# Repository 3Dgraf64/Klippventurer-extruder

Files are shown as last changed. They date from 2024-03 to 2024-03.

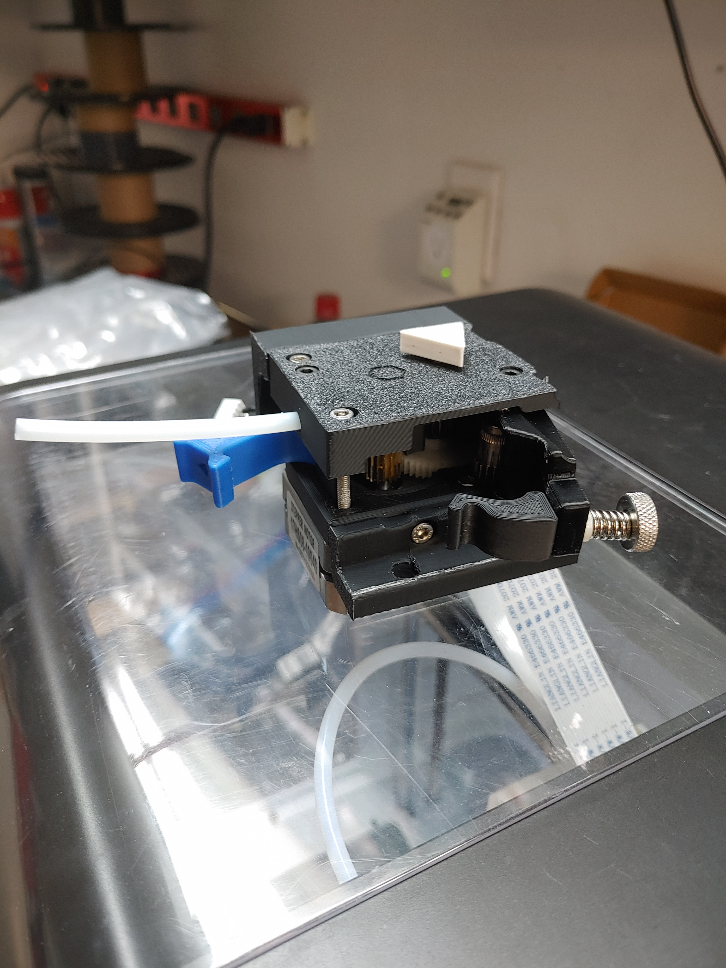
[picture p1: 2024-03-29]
Images/20240329_131136[1].jpg

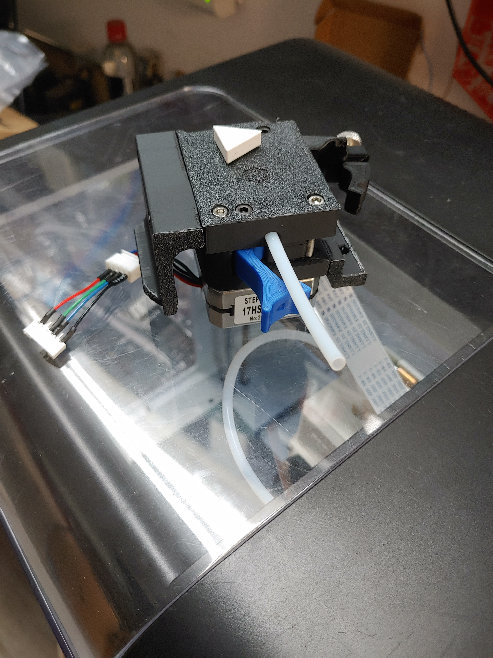
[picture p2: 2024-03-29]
Images/20240329_131118[1].jpg

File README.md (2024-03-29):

# Klippventurer-mods
!!IN PROGRESS!!

This is my contribution to the Klippventurer project.
A big thank you to The-Synthax for being involved in this project by giving us the opportunity to replace the firmware of this printer by Klipper.
Check out here: https://github.com/synthread/Klippventurer

In my Adventurer 3 printer upgrade process, the next step after upgrading the operating system to Klipper (Klippventurer) is to replace the extruder.
I had an old Voron Clockwork extruder lying around.  So I decided to go from there.  Original Voron's .step files where edited in FreeCad.
The result is an extruder whose internal parts are those of the Clockwork but whose fasteners are modified.

Printing:

The printing parameters are those prescribed by Voron: ABS, layer height 0.2mm, extrusion width 0.4,
filling 40%, grid type filling..., walls 4, upper/ lower layers 5 and no support.
For the legs I suggest a skirt.  Cut the parts in triangle.  These are supports.

Hardware and assembly:

The hardware and assembly is essentially the same as Voron’s:
https://github.com/VoronDesign/Voron-Afterburner/blob/afterburner/Manual/Afterburner.pdf
The main differences are the attachment of the legs and an ECAS coupler.
I did an adapter to connect the motor.
The target is held by 2 3x6mm magnets. 

Config:
You'll have to modify your 
rotation_distance: 39.461375 and
gear_ratio: 50:10.  
You may also have to reverse the rotation: dir_pin: !PA2

Tests:
Preliminary test shows 15mm3/sec with a .4mm CHT nozzle at 225 degc PLA

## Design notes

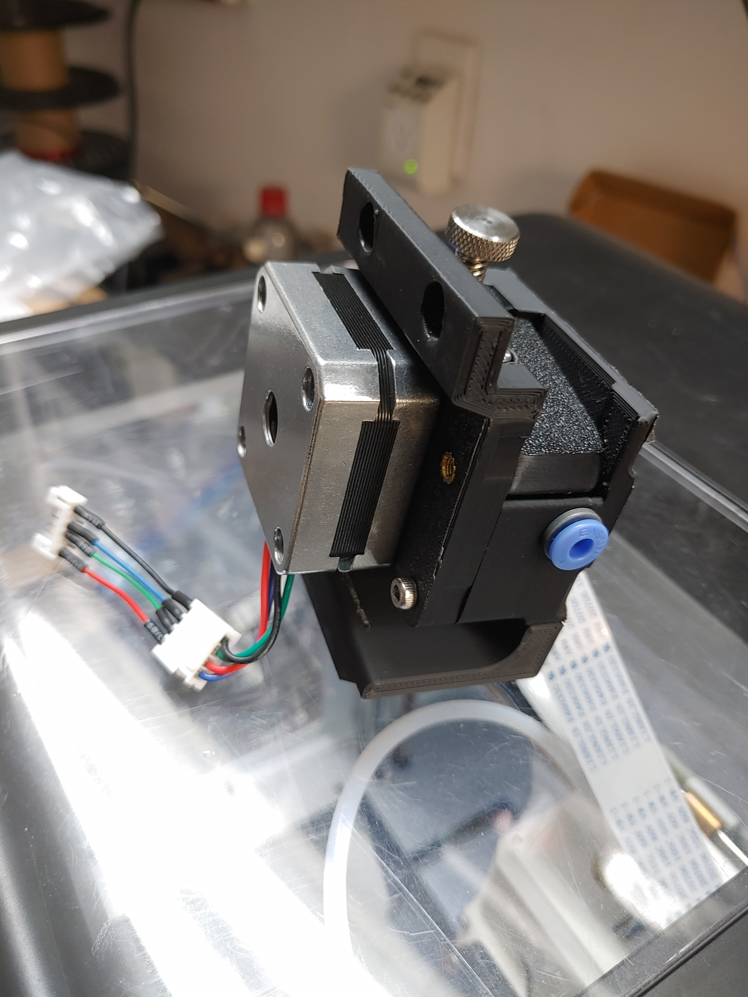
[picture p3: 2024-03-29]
Images/20240329_131154[1].jpg

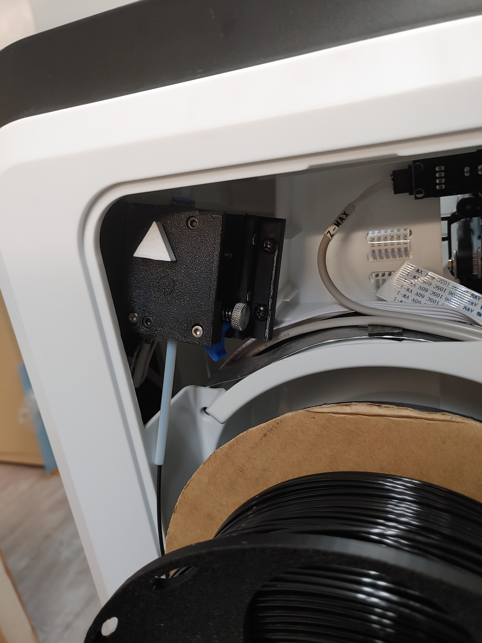
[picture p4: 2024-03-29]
Images/20240329_131842[1].jpg

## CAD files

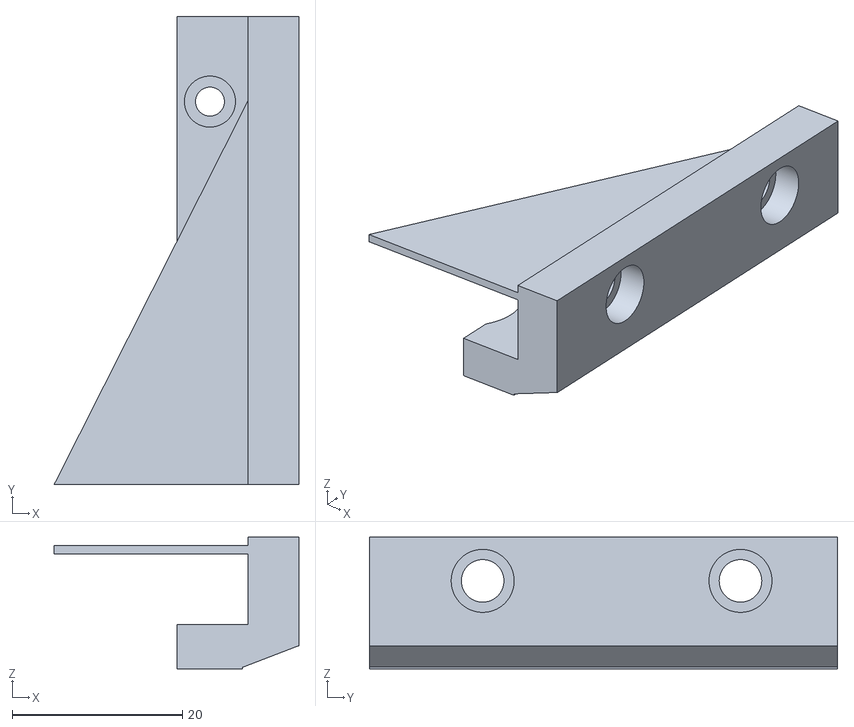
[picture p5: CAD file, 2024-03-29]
STLs/Right leg.stl
28.8 x 55.0 x 15.5

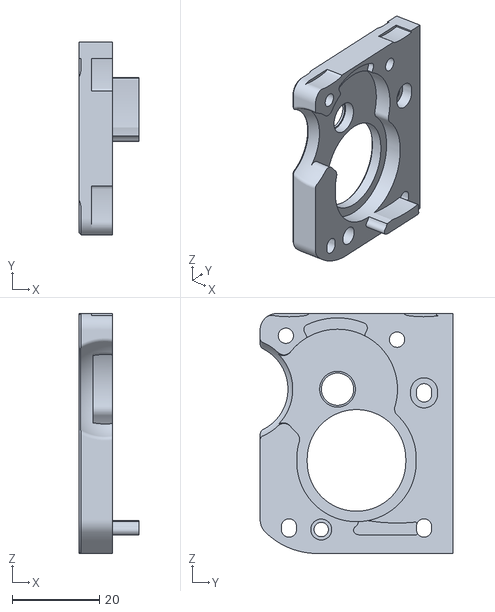
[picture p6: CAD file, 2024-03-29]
STLs/Motor plate.stl
13.7 x 44.2 x 55.0

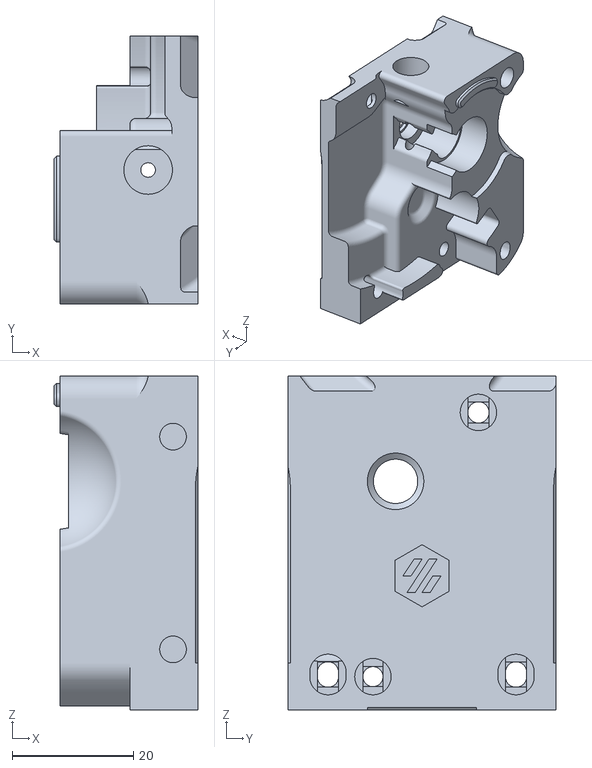
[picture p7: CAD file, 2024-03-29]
STLs/Front body.stl
23.7 x 44.2 x 55.0

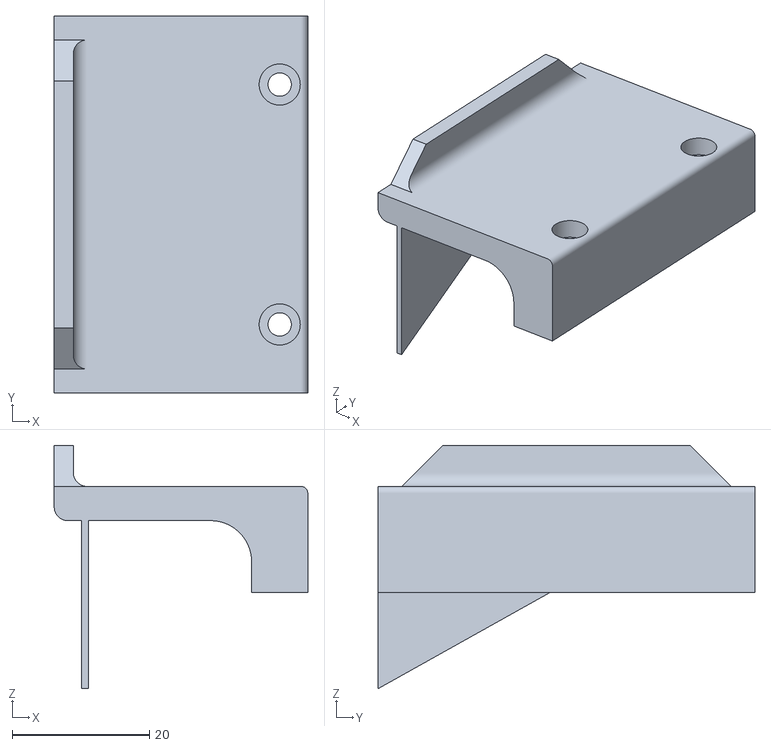
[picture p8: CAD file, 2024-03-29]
STLs/Left leg.stl
37.0 x 55.0 x 35.5

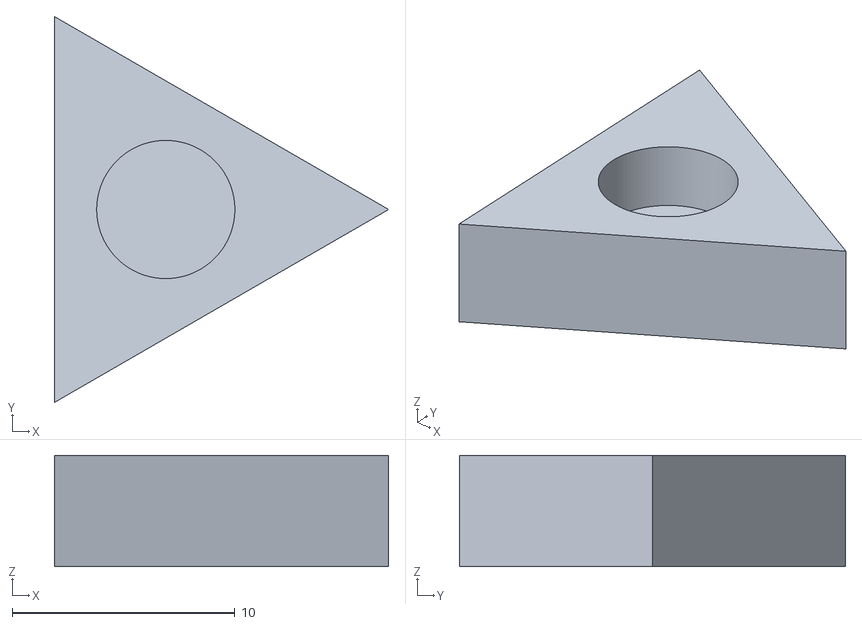
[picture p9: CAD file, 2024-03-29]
STLs/Target.stl
15.0 x 17.3 x 5.00

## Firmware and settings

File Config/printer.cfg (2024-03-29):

# This file contains pin mappings for Adventurer 3 and MonoPrice Voxel with SZ16 mainboard
# There may be versions of these printers that require slight modifications to the config.
# To use this config, the firmware should be compiled for the STMicroelectronics STM32,
# Processor model STM32F103, Clock Reference 12 MHz crystal, Serial on USART1 PA10/PA9.
# To install Klipper, you must follow the steps as described here:
# https://github.com/synthread/Klippventurer

# See docs/Config_Reference.md for a description of parameters.
# If you have TMC2209 drivers (like Adventurer 3 Pro) replace all instances of TMC2208 in this config with TMC2209
[include adv3-macros.cfg]
[include fluidd.cfg]
[include KAMP_Settings.cfg]
[exclude_object]

[mcu]
serial: /dev/ttyAMA0
baud: 250000
restart_method: command
#[mcu rpi]
#serial: /tmp/klipper_host_mcu

[printer]
kinematics: cartesian
max_velocity: 800
square_corner_velocity: 6
max_accel: 6500
max_z_velocity: 30
max_z_accel: 400

[stepper_x]
step_pin: PB8
dir_pin: !PB9
enable_pin: !PB7
microsteps: 32
rotation_distance: 33.9
endstop_pin: ^PC14
position_endstop: 159 # Set this to the distance between the endstop trigger point and touching the left side of the axis
position_max: 161 # Set this to the distance between the endstop and touching the right side of the axis, PLUS position_endstop
position_min: 0 # Leave this alone
homing_speed: 75

[stepper_y]
step_pin: PC1
dir_pin: !PC2
enable_pin: !PC0
microsteps: 32
rotation_distance: 33.9
endstop_pin: ^PB3
position_endstop: 4 # Set this to the distance between the endstop trigger point and touching the back side of the axis
position_max: 151 # Set this to the distance between the endstop and touching the front side of the axis
homing_speed: 75

[stepper_z]
step_pin: PC8
dir_pin: !PC9
enable_pin: !PC7
microsteps: 16
rotation_distance: 6.25
endstop_pin: !PC13
position_min: -2 # This is slightly lower than the bed surface to allow for mesh leveling
#position_endstop: 148 # Leave this alone, use fluidd to calibrate your Z offset.
position_max: 155 # Set this to the distance between the endstop trigger point and touching the top of the axis. If you see the axis skew diagonally at this position, it's too high
homing_speed: 25
second_homing_speed: 15

[thermistor adv3_ntc]
temperature1: 19
resistance1:  123000
temperature2: 79
resistance2:  5820 
temperature3: 230
resistance3:  255 

[extruder]
step_pin: PA1
dir_pin: !PA2
enable_pin: !PA3
microsteps: 16
full_steps_per_rotation: 200
gear_ratio: 50:10
rotation_distance: 39.461375
nozzle_diameter: 0.4
filament_diameter: 1.750
heater_pin: PA8
max_power: 0.8
sensor_type: ATC Semitec 104NT-4-R025H42G
sensor_pin: PA5
min_temp: 10
max_temp: 270
min_extrude_temp: 10
#control = pid
#pid_kp = 26.213
#pid_ki = 1.304
#pid_kd = 131.721
max_extrude_only_distance: 550
max_extrude_only_velocity: 2000
max_extrude_cross_section: 5
pressure_advance: 1.2
pressure_advance_smooth_time: 0.1

[heater_bed]
heater_pin: PC6
sensor_type: adv3_ntc
sensor_pin: PC4
min_temp: 0
max_temp: 110

[temperature_sensor mcu_temp]
sensor_type: temperature_mcu
#this is the operational temperature range of STM32f103
min_temp: -40
max_temp: 85
[temperature_sensor Pi_2W]
sensor_type: temperature_host
min_temp: 10
max_temp: 100
# Part cooling fan and heatbreak fan
#[fan]
#pin: PB10
#cycle_time: 0.1
[heater_fan Fan_hotend]
##	Hotend Fan - CNC_FAN1
pin: PB10
max_power: 1.0
kick_start_time: 0.5
heater: extruder
heater_temp: 50.0
##	If you are experiencing back flow, you can reduce fan_speed
shutdown_speed:1.0

# Mainboard cooling fan
[controller_fan mainboard]
pin: PA4
heater: extruder, heater_bed

# Chamber ventilation fan
#[fan_generic chamber_fan]
#pin: PB13
#cycle_time: 0.1

[output_pin led]
pin: PB12
value: 1
pwm: true
cycle_time: 0.008333 # This PWM frequency should stop the LED from flickering on video

[homing_override]
axes: zxy
gcode:
 g28 z
 g28 x
 g28 y

[bed_mesh]
speed: 100
horizontal_move_z: 5
mesh_min: 5, 5
mesh_max: 150, 145
probe_count: 3, 3
fade_start: 1
fade_end: 10
fade_target: 0

[input_shaper]
shaper_freq_x: 205
shaper_type: mzv
shaper_freq_y: 197.126
shaper_type: ei

[firmware_retraction]
retract_length: 3.8
retract_speed: 25
unretract_extra_length: 0
unretract_speed: 25

########################################
# TMC2208 configuration
########################################

[tmc2208 stepper_x]
uart_pin: PC10
select_pins: !PB0, !PB1, !PD1
run_current: 0.600
sense_resistor: 0.220
stealthchop_threshold: 999999

[tmc2208 stepper_y]
uart_pin: PC10
select_pins: PB0, !PB1, !PD1
run_current: 0.600
sense_resistor: 0.220
#we use SpreadCycle on this axis due to the weight of the bed and print.

[tmc2208 stepper_z]
uart_pin: PC10
select_pins: !PB0, PB1, !PD1
run_current: 0.600
sense_resistor: 0.220
stealthchop_threshold: 999999

[tmc2208 extruder]
uart_pin: PC10
select_pins:  PB0,  PB1, !PD1
run_current: 0.700
sense_resistor: 0.220

#*# <---------------------- SAVE_CONFIG ---------------------->
#*# DO NOT EDIT THIS BLOCK OR BELOW. The contents are auto-generated.
#*#
#*# [extruder]
#*# control = pid
#*# pid_kp = 10.338
#*# pid_ki = 0.489
#*# pid_kd = 54.660
#*#
#*# [heater_bed]
#*# control = pid
#*# pid_kp = 73.181
#*# pid_ki = 2.957
#*# pid_kd = 452.807
#*#
#*# [stepper_z]
#*# position_endstop = 150.820
#*#
#*# [bed_mesh default]
#*# version = 1
#*# points =
#*# 	-0.088984, 0.127813, 0.323125
#*# 	0.037969, 0.155156, 0.278203
#*# 	0.049688, 0.164922, 0.266484
#*# x_count = 3
#*# y_count = 3
#*# mesh_x_pps = 2
#*# mesh_y_pps = 2
#*# algo = lagrange
#*# tension = 0.2
#*# min_x = 5.0
#*# max_x = 150.0
#*# min_y = 5.0
#*# max_y = 145.0
